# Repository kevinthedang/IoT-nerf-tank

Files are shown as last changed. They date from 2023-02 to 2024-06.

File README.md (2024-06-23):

<div align="center">
    <h1>IoT Nerf Tank</h1>
    <h3>Destruction on Treads and Money well spent</h3>
    <p>
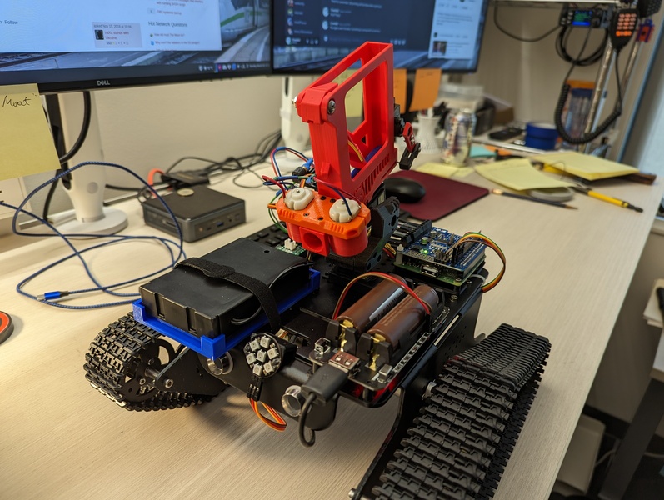
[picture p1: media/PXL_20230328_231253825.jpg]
tank
    
</div>

## Table of Contents
* [Description](#description)
* [Libraries](#libraries--modules)
* [To Run](#to-run--test)
* [Commands](#commands)
* [Parts](#parts)
* [Credit](#credit)

## Description
For this project, we were inspired to combine a tank chassis with a nerf turret to create a tank that will be connected to a web server. The server will send json messages to certain topics on AWS where the tank (Raspberry Pi) will receive the messages through a proxy and execute the parsed commands.

## Libraries / Modules
* Front-End
    * [React](https://react.dev/)
    * [Vite](https://vitejs.dev/)
    * [Axios](https://axios-http.com/docs/intro)
* Back-end
    * [aws-iot-device-sdk](https://github.com/aws/aws-iot-device-sdk-js)
    * [Cors](https://developer.mozilla.org/en-US/docs/Web/HTTP/CORS)
    * [Express](http://expressjs.com/en/starter/installing.html)
* AWS-Tank Proxy:
    * [awscrt](https://pypi.org/project/awscrt/)
    * command_line_utils.py
        * [awsiot-python-sdk](https://github.com/aws/aws-iot-device-sdk-python-v2)
            * `mqtt_connection_builder.py` (should be in the `awsiot` directory)
                * If there is a error on call, the proxy could also depend on `mqtt5_client_builder.py`
* Tank Controller
    * [RPI.GPIO](https://pypi.org/project/RPi.GPIO/)
    * [gpiozero](https://pypi.org/project/gpiozero/)
    * [paho-mqtt](https://pypi.org/project/paho-mqtt/)

## To Run / Test
* Get the [SDK](https://github.com/aws/aws-iot-device-sdk-python) onto the pi and have certificates ready from aws to run commands to the pi from the client
    * create folder in the `~` directory called `certs` and place all of your certification files in there.
    * You will need to run a certain command in the `ClientToJoxConnectionProxy` directory.
        * `python3 internetJox.py --topic <your topic-name> --ca_file ~/certs/AmazonRootCA1.pem --cert ~/certs/certificate.pem.crt --key ~/certs/private.pem.key --endpoint <your aws endpoint here>`
            * You can also you the topic that the server uses: `from_client`.
    * You will also need to run another command in a seperate terminal called `RobotJoxControl.py` can be found in the `RobotJoxControl` directory
        * Run the file as `./RobotJoxControl.py`.
    * Now the Tank should be able to listen to outside commands:
        * Jox <--- AWSProxy <--- ExternalClient(s)...
    * `internetJox.py` is not required for any other type of control or connection you would like to make with the tank! It is only a sample of a connection from a separate (or same) network client.

* Pull client and server [code](https://github.com/kevinthedang/IoT-nerf-tank) directories
    * You will need to add your certifications into the `server` directory as a folder named `certifs`
    * You will also need a json file named `endpoint.json` to hold your endpoint for the server to connect to:
        * i.e. `{ "endpoint": "<your_endpoint_here>" }`
    * NodeJs must be install to run the client and sever
        * go into the `client` directory and run `npm i` then `npm start`
        * go into the `server` directory and run `npm i` then `npm start`
        * not the server should be up at `localhost:5173` most likely (or whatever vite tells you its hosted at)
    * Now you can click on the buttons and the Pi should receive the messages!
    * Jox <--- AWSProxy <--- ExpressClient <---> UserClient

## Commands
* There are not too many commands for the Tank to run, but knowing them can help customize how they can run (either from the proxy or from default calls)
    * Treads:
        * "leftTread:drive:`<value between -1 to 1>`"
        * "rightTread:drive:`<value between -1 to 1>`"
    * Turret: 
        * To fire the turret, call commands in order:
            * "flywheel:fire"
            * "ammoRammer:fire"
        * Turret Elevation:
            * "gunElevator:`<"up" or "down">:`:`<degrees>`"
                * The current degrees cannot exceed 90
        * Turret Left / Right:
            * "turretRing:`<"turnRight" or "turnLeft">`:`<degrees>`"
                * The current degrees cannot exceed 90
        * Targeting Laser:
            * "targetingLaser:`<"on" or "off">`"
        * Some commands can be set to 0 degrees (home angle):
            * "`<"gunElevator" or "turretRing">`:setHome"

## Parts
* Refer to: 
    * `Parts_List.xlsx` in the `extras` folder for all the turret parts bought
    * [Bluetooth Nerf Turret - Hardware](https://www.littlefrenchkev.com/bluetooth-nerf-turret/#comp-k1tpv8jv)
    * [SZDoit Black T300 Tank Chassis](https://www.amazon.com/SZDoit-Raspberry-Learning-Caterpillar-Platform/dp/B08HRTZNHW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) (Alternative and cheaper options for chassis are fine too)
    * [Raspberry Pi](https://www.adafruit.com/product/4296)
    * Also Refer to `3D printing parts` for other parts to for mounting
    * [Adafruit DC and Stepper Motor HAT for Raspberry Pi](https://www.adafruit.com/product/2348)
        * [Documentation](https://learn.adafruit.com/adafruit-dc-and-stepper-motor-hat-for-raspberry-pi/using-dc-motors) for use

## Credit
* [Kole Davis](https://github.com/Kole0518)
* [Drew Bogdan](https://github.com/DrewBogdan)
* [Vincent Do](https://github.com/VinnyVinVince)
* [Kevin Dang](https://github.com/kevinthedang)
* [Aaron Crandall](https://github.com/acrandal)

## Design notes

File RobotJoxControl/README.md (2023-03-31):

# Robot Jox onboard hardware service

Suite of objects representing and limiting/controlling the Robot Jox robot.
These include motors, servos, lights, and a targeting laser.

This package is designed to be run as a systemd service - see Makefile

### Contributors:
Aaron S. Crandall \<crandall@gonzaga.edu>

### Copyright
2023

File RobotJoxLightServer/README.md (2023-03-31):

# Robot Jox Light Server for RGB LED strip

System service for controlling the RGB LED light strip.
It listens on an MQTT topic for control messages and runs the strip from those.
See message options and formats below for documentation.

See Makefile for install, dependencies, and service start/stop controls.

### MQTT settings:

- host: localhost  
- topic: lights

### Message types and formats:

- "blankLights"
    - Will blank out (turn off) the whole strip

- "setPixel"
    - Sets a single pixel a provided RGB color
    - index: pixel strip led index
    - R,G,B: values of 0..255 for the light values to set the pixel
    - format: "setPixel:index:R:G:B"
    - example: "setPixel:3:150:150:0"

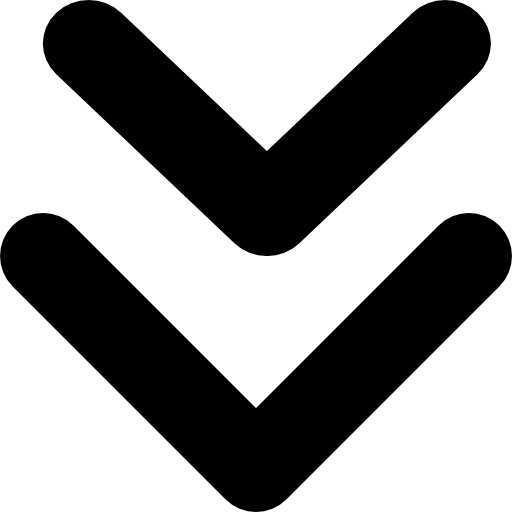
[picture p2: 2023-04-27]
client/src/style/images/down-double.png

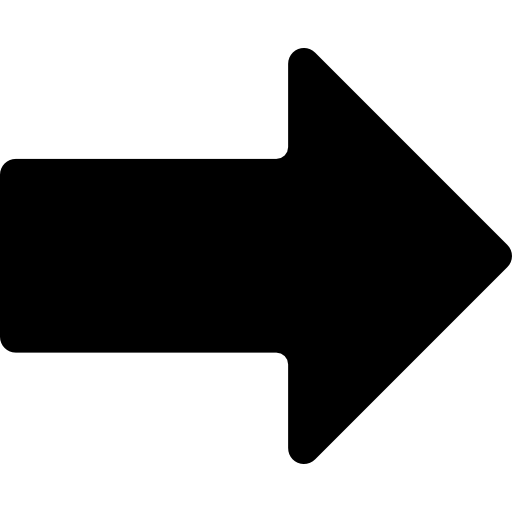
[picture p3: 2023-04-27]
client/src/style/images/right-arrow.png

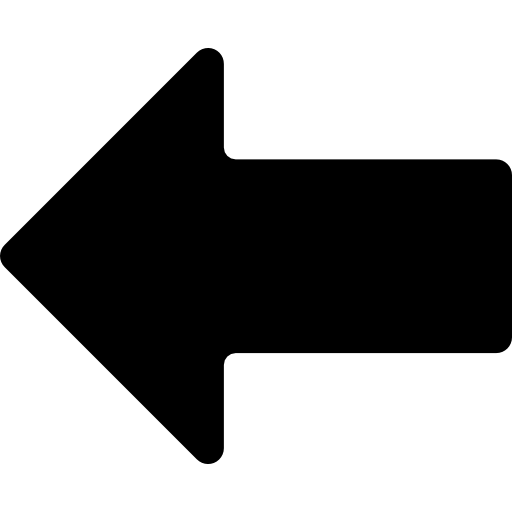
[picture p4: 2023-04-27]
client/src/style/images/left-arrow.png

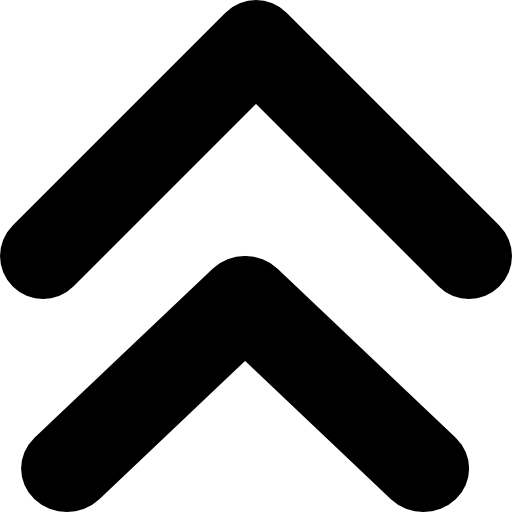
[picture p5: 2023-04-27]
client/src/style/images/up-double.png

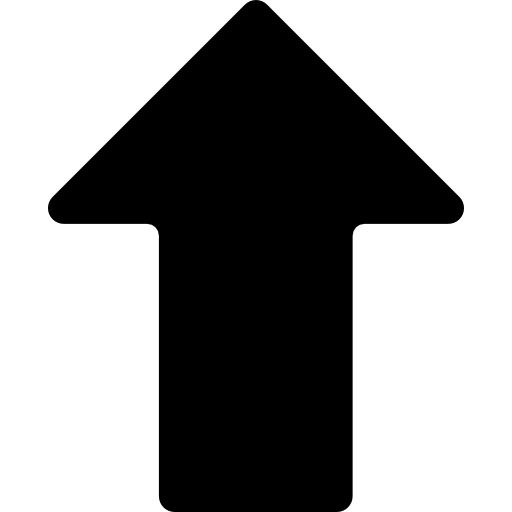
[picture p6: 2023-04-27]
client/src/style/images/up-arrow.png

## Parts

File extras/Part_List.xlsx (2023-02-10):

Parts List
Part | amount | Price | Link
M5x20 Countersunk Screws (4) | 4 (pack) | 1.68 | M5 X 20mm Socket Countersunk Screws (DIN 7991) - High Tensile Steel (10.9) (accu.co.uk) (https://www.accu.co.uk/countersunk-socket-head-screws/472033-SSK-M5-20-10-9?google_shopping=1&c=2)
M2x10 Self Taping Screws (40) | 1 (pack) | 8.99 | https://www.amazon.com/uxcell-M2x10mm-Thread-Button-Socket/dp/B01AXUSN1Y?hvadid=167128911295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
1.5mm metal rod | 5 (pack) | 8 | https://www.amazon.com/dp/B07KY8XJQL?s=hi&sp_csd=d2lkZ2V0TmFtZT1zcF9kZXRhaWxfdGhlbWF0aWM (https://www.aliexpress.us/item/3256803590822918.html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)
Dupont Connector Set | 1 | 10 | https://www.amazon.com/Dupont-Connector-Kit-Connectors-Plusivo/dp/B078RRPRQZ?hvadid=241994846339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
type 130 dc motors (rated 9v) (2) | 2 | 4 | https://www.adafruit.com/product/711
LM2596 Buck Converter(1) | 1 | 4.9 | https://www.digikey.com/en/products/detail/dfrobot/DFR0379/7087190
MG996r Servos(2) | 2 | 21 | https://www.amazon.com/MG996R-Aideepen-Torque-Digital-Helicopter/dp/B09YT48XC7
FR207 Rectifier Diode(1) | 1 | 0.18 | https://www.digikey.com/en/products/detail/smc-diode-solutions/FR207/5993212
RFP30N06LE Mosfet (1) | 1 | 2.43 | https://www.digikey.com/en/products/detail/onsemi/HUF76423P3/1055344
Chassis | 1 | 50 | https://www.amazon.com/SZDoit-Raspberry-Learning-Caterpillar-Platform/dp/B08HRTZNHW
Total |  | 111.18

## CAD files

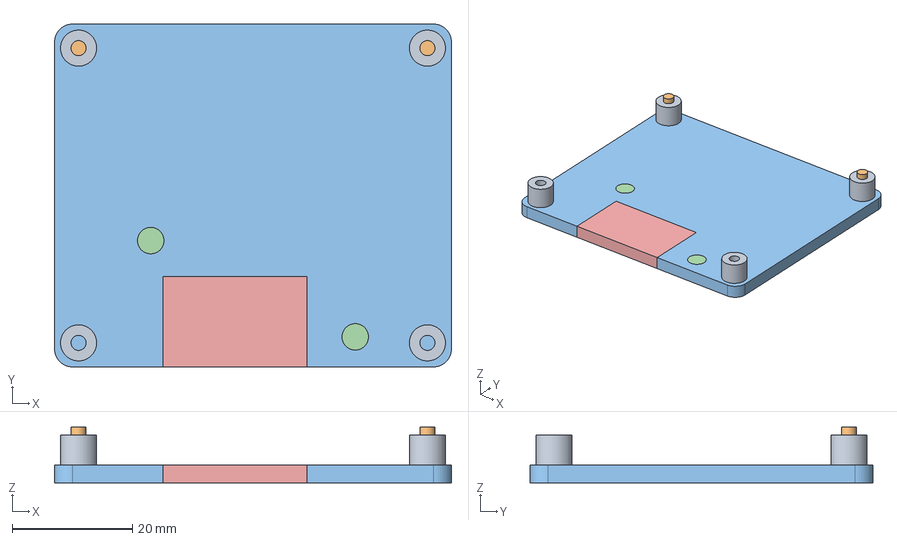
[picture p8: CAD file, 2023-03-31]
3D printing parts/CAD Parts/RPiMount.FCStd
66.0 x 57.0 x 9.30 mm
Mounting Holes

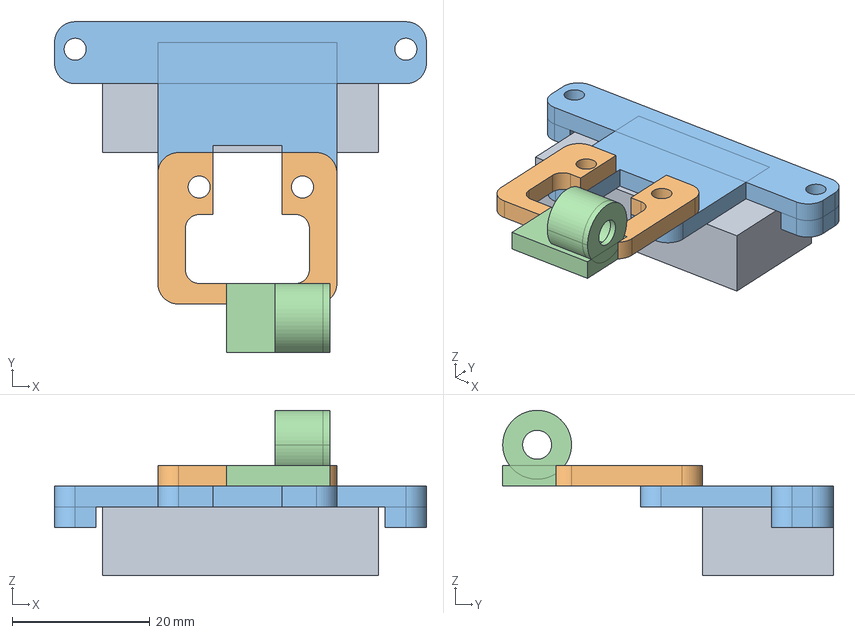
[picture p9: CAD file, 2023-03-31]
3D printing parts/CAD Parts/Turret Wiring Clamp.FCStd
54.0 x 48.0 x 24.0 mm
Wiring Clamp
Top Bracket II
Laser Mount

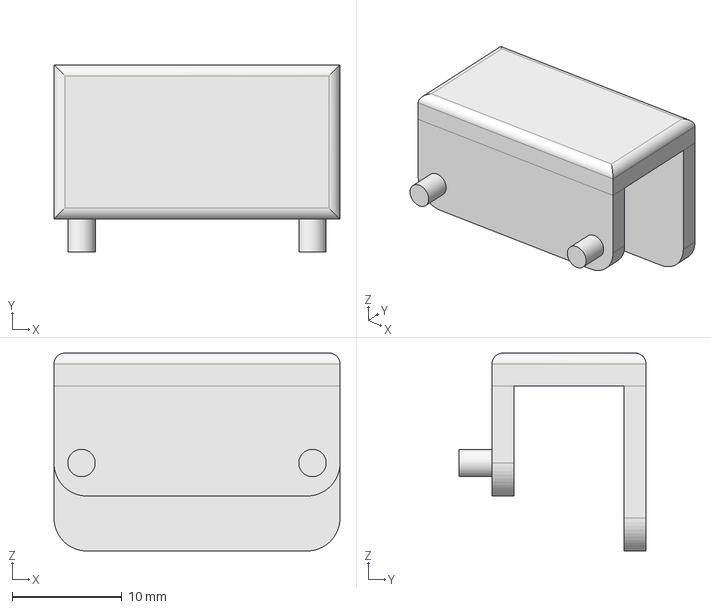
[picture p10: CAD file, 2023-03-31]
3D printing parts/CAD Parts/Headlight Holder.FCStd
26.0 x 17.0 x 18.0 mm

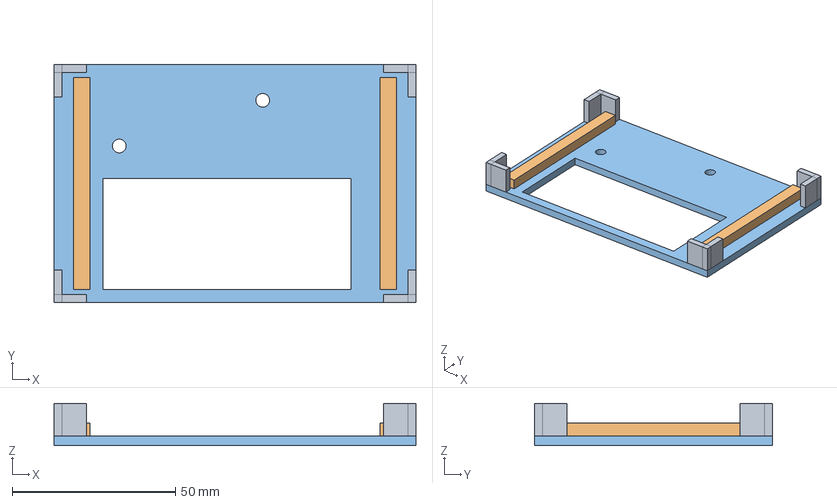
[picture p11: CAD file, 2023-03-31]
3D printing parts/CAD Parts/MotorPowerMount.FCStd
111.0 x 73.0 x 13.0 mm
Corner Holders
Standoff Rails

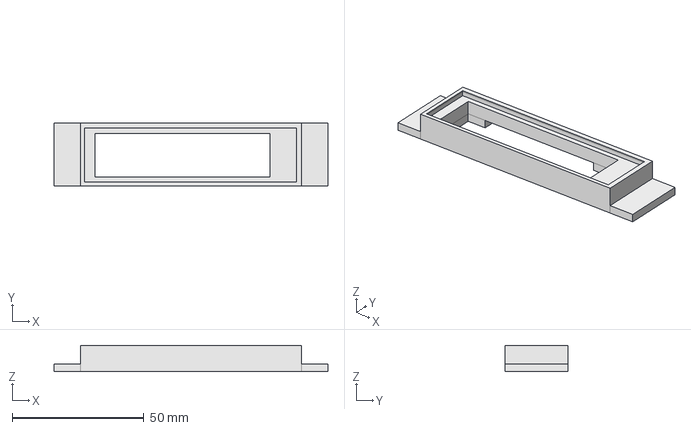
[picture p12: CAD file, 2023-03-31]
3D printing parts/CAD Parts/PowerBoxHolder.FCStd
104.0 x 24.0 x 10.0 mm

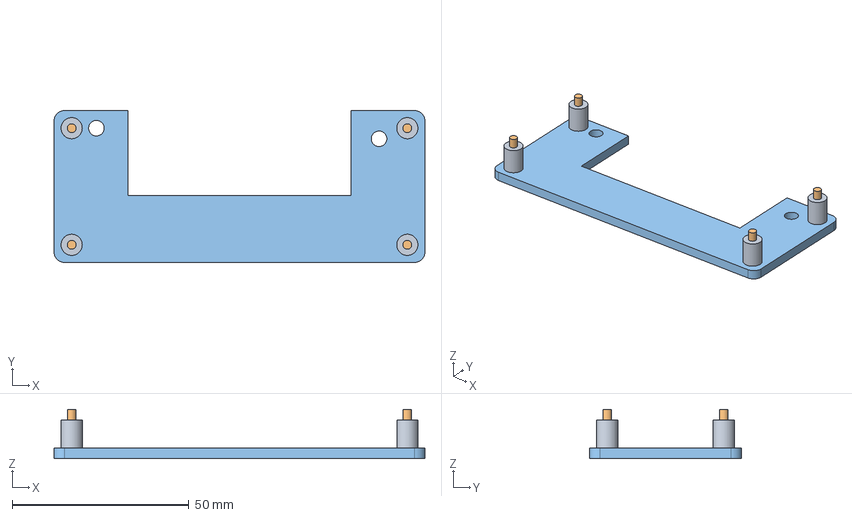
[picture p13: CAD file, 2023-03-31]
3D printing parts/CAD Parts/PiPowerMount.FCStd
105.0 x 43.0 x 14.0 mm
Standoffs
Standoffs001

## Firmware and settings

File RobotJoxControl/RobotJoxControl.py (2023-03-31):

#!/usr/bin/python3
"""
Main program for the Robot Jox hardware control service

Author: Aaron S. Crandall <crandall@gonzaga.edu>
Project: Robot Jox IoT NERF Robot
Copyright: 2023
"""

# Built-in Python libs
import logging
from time import sleep

# Special Project depencies
import board
from adafruit_motorkit import MotorKit
import paho.mqtt.client as mqtt
import RPi.GPIO as GPIO

# Project Classes
from TargetingLaser import TargetingLaser
from TreadMotor import TreadMotor
from GunElevator import GunElevator
from AmmoRammer import AmmoRammer
from TurretRing import TurretRing
from Flywheel import Flywheel


# ***************************************************************** #
def on_mqtt_message(client, userdata, message):
    """
    Callback function that is executed when a message is received from the MQTT broker.

    :param client: The MQTT client instance.
    :type client: paho.mqtt.client.Client
    :param userdata: The user data passed to the callback.
    :param message: An object containing the message payload, topic, QoS, and retain flag.
    :type message: paho.mqtt.client.MQTTMessage
    """
    message = message.payload.decode()
    message = message.strip()
    logging.debug(f"Control: {message}")

    commandFields = message.split(":")
    deviceName = commandFields[0]
    commandType = commandFields[1]
    commandOptions = commandFields[2:]

    if deviceName in robotDevices:
        robotDevices[deviceName].command(commandType, commandOptions)
    else:
        logging.warn(f"Control of unknown device: {deviceName} - {message}")


def setupMQTTClient() -> mqtt.Client:
    """
    Sets up and returns an instance of the MQTT client.

    :return: An instance of the MQTT client.
    :rtype: paho.mqtt.client.Client
    """
    mqttClient = mqtt.Client()
    mqttClient.connect("localhost", 1883)
    mqttClient.subscribe("control")
    mqttClient.on_message = on_mqtt_message
    return mqttClient


def setupRobotDevices() -> dict:
    """
    Sets up and returns a dictionary of the robot's devices.

    :return: A dictionary containing the robot's devices.
    :rtype: dict
    """
    global robotDevices
    motorKit = MotorKit(i2c=board.I2C())

    leftTread = TreadMotor(motorAPI=motorKit.motor3, name="left")
    rightTread = TreadMotor(motorAPI=motorKit.motor4, name="right")
    flywheel = Flywheel(
       motorAPIRightFlywheel=motorKit.motor1, motorAPILeftFlywheel=motorKit.motor2
    )
    targetingLaser = TargetingLaser(gpio_pin=5)
    turretRing = TurretRing(gpio_pin=12)
    gunElevator = GunElevator(gpio_pin=13)
    ammoRammer = AmmoRammer(gpio_pin=16)

    robotDevices["leftTread"] = leftTread
    robotDevices["rightTread"] = rightTread
    robotDevices["flywheel"] = flywheel
    robotDevices["targetingLaser"] = targetingLaser
    robotDevices["turretRing"] = turretRing
    robotDevices["gunElevator"] = gunElevator
    robotDevices["ammoRammer"] = ammoRammer

    return robotDevices


# ************************************************************************** #
if __name__ == "__main__":
    global robotDevices
    robotDevices = {}

    FORMAT = "%(asctime)s.%(msecs)03d;%(levelname)s;%(name)s:%(message)s"
    logging.basicConfig(format=FORMAT, level=logging.DEBUG, datefmt="%H:%M:%S")

    logging.info("Log started")

    mqttClient = setupMQTTClient()
    robotDevices = setupRobotDevices()

    try:
        mqttClient.loop_forever()
    except KeyboardInterrupt:
        logging.info("Received keyboard interrupt - quitting.")
    finally:
        mqttClient.disconnect()

        robotDevices["leftTread"].stop()
        robotDevices["rightTread"].stop()

    logging.info("Done.")

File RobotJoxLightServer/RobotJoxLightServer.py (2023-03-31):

#!/usr/bin/python3
#
#   RGB LED lights strip server
#   MQTT message API
#
# Constributors:
#  Aaron S. Crandall <crandall@gonzaga.edu>
#
# Copyright 2023
#

import logging
import time


import board
import neopixel
import paho.mqtt.client as mqtt

PIXEL_STRIP_PIN = board.D21
PIXEL_LIGHTS_COUNT = 8
PIXEL_RGB_ORDER = neopixel.GRB


# ****************************************************#
def on_mqtt_message(client, userdata, message):
    message = message.payload.decode()
    message = message.strip()
    logging.debug(f"lights: {message}")

    handle_lights_message(message)


def handle_lights_message(message: str):
    global pixels
    # blankLights
    if message.startswith("blankLights"):
        blankStrip(pixels)
    # setPixel:index:R:G:B
    elif message.startswith("setPixel"):
        vals = message.split(":")
        index = int(vals[1])
        red = int(vals[2])
        green = int(vals[3])
        blue = int(vals[4])
        # logging.debug(f"index: {index} = ({red},{green},{blue})")
        pixels[index] = (red, green, blue)
        pixels.show()
    

def blankStrip(pixels):
    pixels.fill((0,0,0,0))
    pixels.show()


def setupMQTTClient():
    mqttClient = mqtt.Client()
    mqttClient.connect("localhost", 1883)
    mqttClient.subscribe("lights")
    mqttClient.on_message = on_mqtt_message
    return mqttClient


def setupLEDStrip():
    global pixels
    pixels = neopixel.NeoPixel(
        PIXEL_STRIP_PIN, PIXEL_LIGHTS_COUNT, brightness=0.2, auto_write=False, pixel_order=PIXEL_RGB_ORDER
    )
    blankStrip(pixels)
    logging.info("LED Pixel strip connected")
    return pixels



# ********************************************************#
if __name__ == "__main__":
    global pixels

    FORMAT = '%(asctime)s.%(msecs)03d;%(levelname)s;%(name)s:%(message)s'
    logging.basicConfig(format=FORMAT, level=logging.DEBUG, datefmt='%H:%M:%S')

    setupLEDStrip()
    mqttClient = setupMQTTClient()

    pixels[1] = (0,255,0)
    pixels.show()

    logging.info("System setup - starting main loop")
    try:
        mqttClient.loop_forever()
    except KeyboardInterrupt:
        logging.info("Received interrupt - quitting")
    finally:
        mqttClient.disconnect()

    logging.info("Done.")

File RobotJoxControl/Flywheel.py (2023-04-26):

"""
Module: Flywheel
Author: Aaron S. Crandall <crandall@gonzaga.edu>
Project: Robot Jox IoT NERF Robot
Copyright: 2023

This module defines the Flywheel class that controls the motors
of the flywheels on the NERF robot.
"""

import logging
import threading
from time import sleep, time


class Flywheel:
    def __init__(self, motorAPIRightFlywheel, motorAPILeftFlywheel):
        """
        Initializes the Flywheel object.

        Args:
            motorAPIRightFlywheel (MotorAPI): Right motor API for the flywheel.
            motorAPILeftFlywheel (MotorAPI): Left motor API for the flywheel.
        """
        name = "Flywheel"
        self.log = logging.getLogger(name=__class__.__name__ + "-" + name)

        self.motorAPIRightFlywheel = motorAPIRightFlywheel
        self.motorAPILeftFlywheel = motorAPILeftFlywheel
        self.name = name
        self.log.info(f"Created Flywheel: {name}")

        # Default motor speeds
        self.fireSpeed = 1.0
        self.offSpeed = 0.0
        self.readySpeed = 0.5

        # Deadman switch timeout
        self.deadmanTimeout = 5.0
        self.lastControlEpoch = time()
        self.deadmanRunning = False
        self.deadmanThread = None

    def drive(self, speed=0) -> None:
        """
        Sets the motor speeds for the flywheel.

        Args:
            speed (float): Speed to set for the motors (default 0).
        """
        self.log.debug(f"{self.name} speed {speed}")
        self.motorAPIRightFlywheel.throttle = speed
        self.motorAPILeftFlywheel.throttle = 1 * speed
        self.lastControlEpoch = time()
        if not self.deadmanRunning:
            self.deadmanThread = threading.Thread(target=self.deadmanMethod)
            self.deadmanThread.start()

    def stop(self) -> None:
        """Stops the flywheel motors."""
        self.motorAPIRightFlywheel.throttle = self.offSpeed
        self.motorAPILeftFlywheel.throttle = self.offSpeed

    def deadmanMethod(self) -> None:
        """Method for deadman switch to stop motor if no more drive commands arrive."""
        self.deadmanRunning = True
        self.log.debug("Deadman started")
        while self.lastControlEpoch + self.deadmanTimeout >= time():
            sleep(self.deadmanTimeout)
        self.log.debug("Deadman done - stopping motor")
        self.stop()
        self.deadmanRunning = False

    def __del__(self) -> None:
        """Destructor to stop the flywheel motor. Should always stop on destruction."""
        self.stop()

    def goToReady(self) -> None:
        """Sets the flywheel motors to the ready speed."""
        self.log.debug("Going to ready speed")
        self.drive(speed=self.readySpeed)

    def goToFire(self) -> None:
        """Sets the flywheel motors to the firing speed."""
        self.log.debug("Going to fire speed")
        self.drive(speed=self.fireSpeed)

    def command(self, type: str, options: list) -> None:
        """
        Executes the specified command for the flywheel.

        Args:
            type (str): Type of command to execute.
            options (list): List of options for the command.
        """
        if type == "stop":
            self.stop()
        elif type == "ready":
            self.goToReady()
        elif type == "fire":
            self.goToFire()

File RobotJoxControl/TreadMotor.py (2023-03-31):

"""
Class for a motor controlling a tank tread - DC Motor Driven

This class wraps behaviors of the Adafruit RPi Motor Hat.
Allows for driving the motor at a specified speed, as well
as stopping the motor. It also implements a deadman switch
to stop the motor if it hasn't received a control signal
within a certain time frame.

Author: Aaron S. Crandall <crandall@gonzaga.edu>
Project: Robot Jox IoT NERF Robot
Copyright: 2023
"""

import logging
import threading
from time import sleep, time
import threading


class TreadMotor:
    def __init__(self, motorAPI, name: str):
        """
        Constructor for the TreadMotor class.
        :param motorAPI: The Adafruit RPi Motor Hat motor API
        :type motorAPI: object
        :param name: A name to associate with the motor
        :type name: str
        """

        self.log = logging.getLogger(name=__class__.__name__ + "-" + name)

        self.motorAPI = motorAPI
        self.name = name
        self.log.info(f"Created TreadMotor: {name}")

        self.deadmanTimeout = 1.0
        self.lastControlEpoch = time()
        self.deadmanRunning = False
        self.deadmanThread = None

    def drive(self, speed: int = 0) -> None:
        """
        Drives the motor at the specified speed.

        :param speed: The speed at which to drive the motor. Default 0.
        :type speed: float
        """

        self.log.debug(f"{self.name} speed {speed}")
        self.motorAPI.throttle = speed
        self.lastControlEpoch = time()
        if not self.deadmanRunning:
            self.deadmanThread = threading.Thread(target=self.deadmanMethod)
            self.deadmanThread.start()

    def stop(self) -> None:
        """ Stops the motor. """
        self.motorAPI.throttle = 0

    def deadmanMethod(self) -> None:
        """
        Method that monitors the motor for control signals. If no control
        signals are received for a certain amount of time, the motor is stopped.
        """
        self.deadmanRunning = True
        self.log.debug("Deadman started")
        while self.lastControlEpoch + self.deadmanTimeout >= time():
            sleep(self.deadmanTimeout)
        self.log.debug("Deadman done - stopping motor")
        self.stop()
        self.deadmanRunning = False

    def __del__(self) -> None:
        """ Destructor for the TreadMotor class. Stops the motor.  """
        self.stop()

    def command(self, type: str, options: list) -> None:
        """
        Executes a command on the motor.

        :param type: The type of command to execute.
        :type type: str
        :param options: The options to use when executing the command.
        :type options: list
        """
        speed = float(options[0])
        if speed < -1 or speed > 1:
            self.log.warn(f"Speed sent out of range: {speed}")
        elif type == "drive":
            self.drive(speed=float(options[0]))

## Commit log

2023-02-10 started readme
    [Part_List.xlsx]
2023-03-28 updated readme and added buttons to client
2023-03-30 JoxerImplementation (#3)
    * Initial readme for hardware devices ser
    ice
    * Initial import from offline dev
    * Servos for turret work underway, GTG
    * Finished initial RGB LED light service for MQTT-driven light controls
    * Renaming and adding flywheel control classes
    * Massive overhaul on documentation, 3D printing brackets, and starting service configuration work.
    * Requirements and message parsing fixes for Light Server
    * Fixes and temp removals for off-hardware testing
    * Hardware Driver layer and documentation (#2)
    * Fixing function call bugs and handling more bad message formats
    * Fixed service boot ordering for the light service
    * Added 3D printing CAD docum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
    [Headlight Holder.FCStd, MotorPowerMount.FCStd, PiPowerMount.FCStd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]
2023-04-26 burst-fire button

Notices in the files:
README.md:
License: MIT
